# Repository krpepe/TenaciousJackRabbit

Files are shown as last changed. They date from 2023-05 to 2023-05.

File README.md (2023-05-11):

# Tenacious Jack Rabbit

*__This is still a work in progress!__* <br>
<br>
I have everything assembled but have not set up the config yet. I am hoping to have that done by 5-11-23. I have printed all of the parts that I redesigned and they all fit snuggly. If you decide to try this please let me know if you encounter any issues. I will attempt to correct any issues that come up. I will be updating as necessary. I have included Gearbox front, filament block and filament blocks end with supports incase someones printer can't successfully print it without. I printed mine without supports and had very minamal cleanup to get them to fit.

This is based on the awesome work of EtteGit https://github.com/EtteGit/EnragedRabbitProject. I also found inspiration from the awesome work of sneakytreesnake (https://github.com/sneakytreesnake/SturdyBunnyProject).

# Motivation

After doing some research before building the ERCF I found a lot of people saying there was flex in the assembly that was causing issues with operation. The suggestion was to go with the SturdyBunnyProject. This added a 2020 extrusion in place of the 5mm threaded rods. The only down side to this design in my opinion was it changed the print orientation of the filament block from upright to laying sideways which then required supports to print the filament blocks. I decided to change the location of the 2020 extrusion to allow printing the filament block in the designed orientation to be able to print without supports.

# Changes to BOM

|Qty|Description|
|:---:|---|
|1|2020 Extrusion one end with M6 taped hole (1)|
|1|M6x10 BHCS|
|2|M3 T-nuts (2)|
|7|M3x8 SHCS (2)|
|3|M5 T-nuts|
|3|M5x10 BHCS|

* (1) 171mm for 6, 234mm for 9 and 297mm for 12. These are minimum lengths, can be longer if you want.
* (2) Only needed for mounting Fysetc ERB V1.1 to 2020 exrtusion

# Assembly

To assemble you have to attach the 2020 extrusion to the Gearbox_Front_2020_Mount with the M6x10 before assembling the gearbox. The filament blocks and bearing blocks slide on to the 2020 extrusion instead of the 5mm rods in the assembly manual. The Filament_Blocks_End goes on after the last filament block and should be tight against the last filament block. 2 M5 BHCS and M5 T-nuts attach it to the 2020 extrusion. There should be no air gaps between the gearbox front and the Filament Blocks End.

# Assembly Pics





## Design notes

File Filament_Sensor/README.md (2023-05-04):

Readme for Filament Sensor

Clockwoork 2 with 3mm ball bearing, 3mm rod and micro switch.

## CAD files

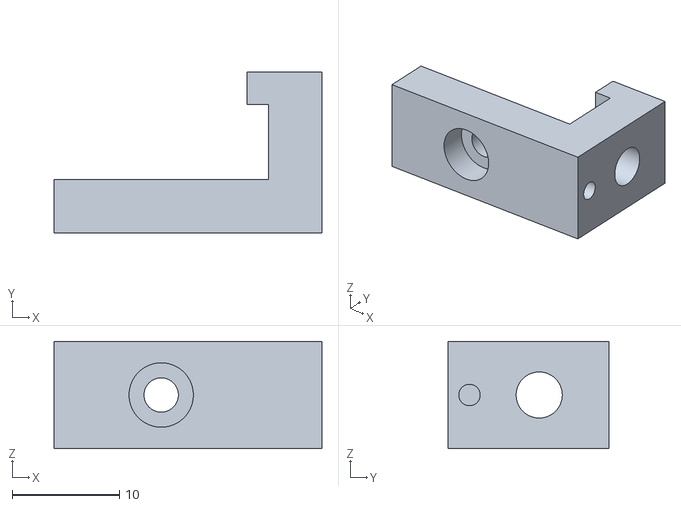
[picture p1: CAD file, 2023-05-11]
Carrot_Feeder/Stls/2020/Fysect_ERB_V1.1_2020_Mount.stl
25.0 x 15.0 x 10.0

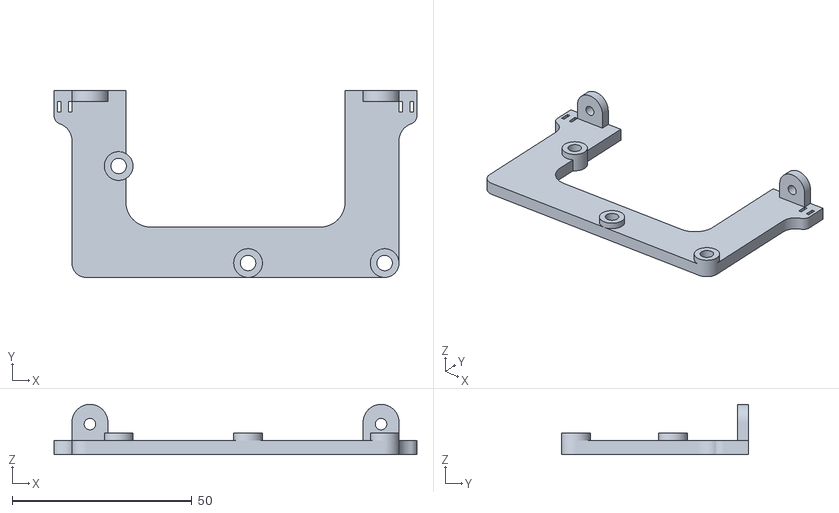
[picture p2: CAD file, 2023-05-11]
Carrot_Feeder/Stls/2020/erb_holder_x2.stl
101.0 x 52.0 x 14.0

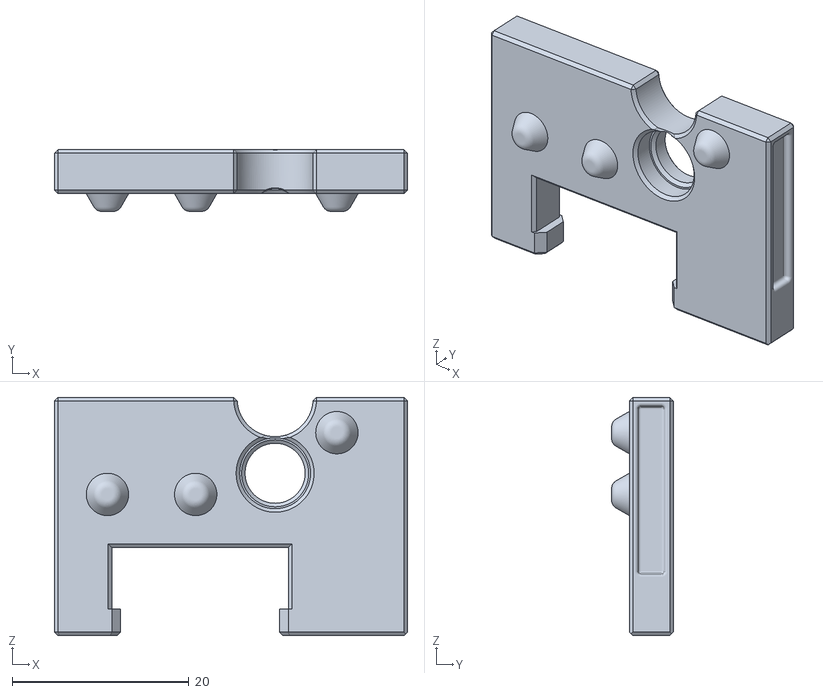
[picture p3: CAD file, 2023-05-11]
Carrot_Feeder/Stls/2020/Bearing insert 2020 mount v3.stl
40.0 x 7.00 x 27.0

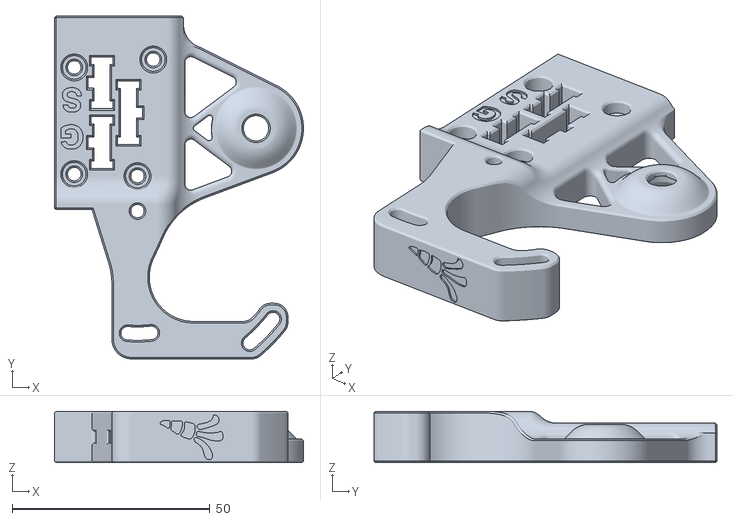
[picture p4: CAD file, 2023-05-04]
Carrot_Feeder/Stls/2020/M4 Gear Arm 2020 mount v4.stl
63.0 x 86.7 x 13.0

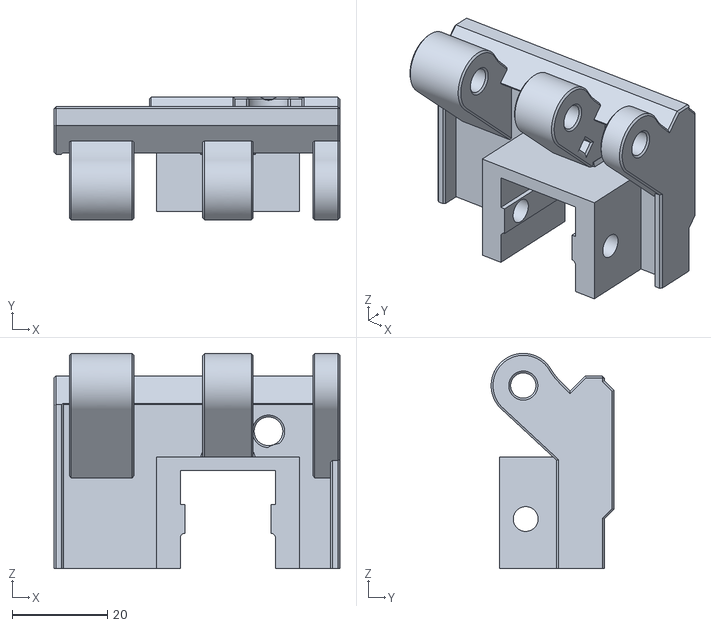
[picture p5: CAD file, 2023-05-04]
Carrot_Feeder/Stls/2020/Filament blocks end 2020 mount v11.stl
60.0 x 25.7 x 45.1

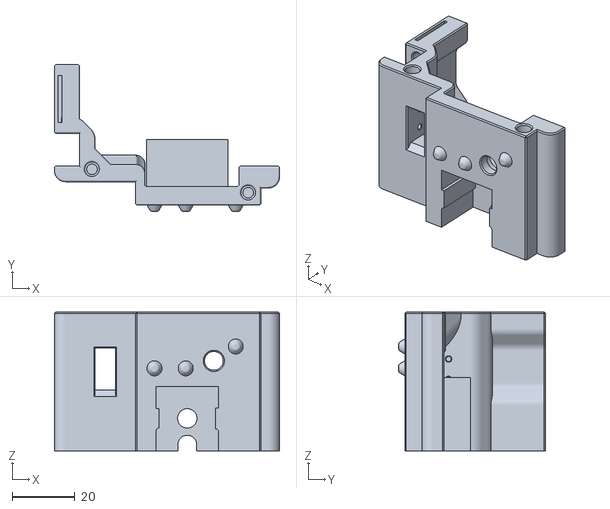
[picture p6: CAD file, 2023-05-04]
Carrot_Feeder/Stls/2020/Gearbox Front 2020 Mount v13.stl
72.0 x 47.0 x 44.4

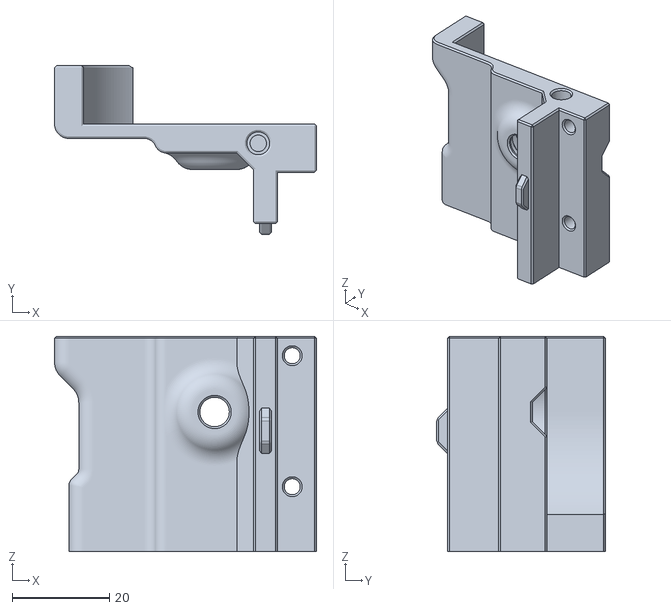
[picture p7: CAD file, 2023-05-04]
Carrot_Feeder/Stls/2020/Gear box mount rear 2020 v6.stl
54.0 x 34.8 x 44.4

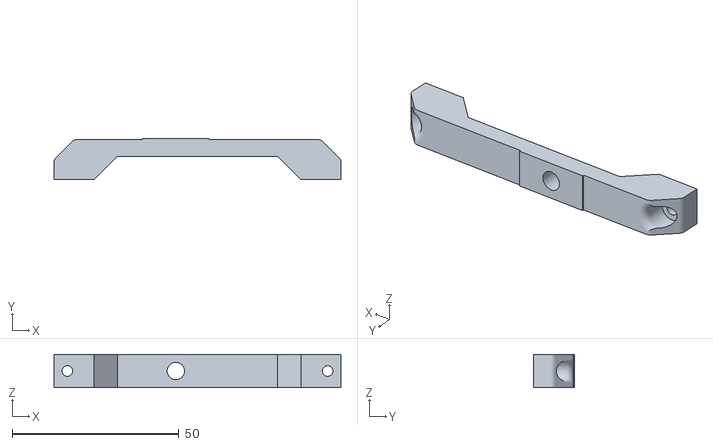
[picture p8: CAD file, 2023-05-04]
Carrot_Feeder/Stls/2020/Outside foot v5.stl
86.0 x 12.4 x 10.0

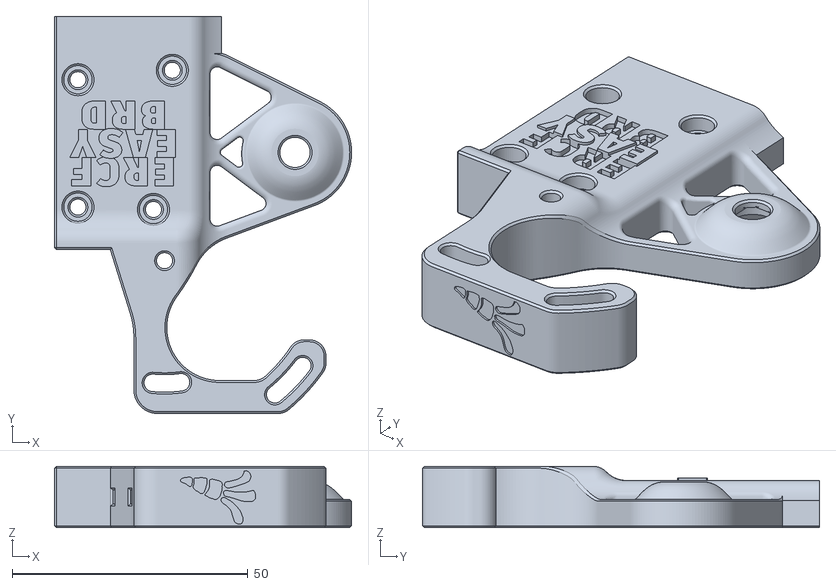
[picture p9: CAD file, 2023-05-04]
Carrot_Feeder/Stls/2020/Motor_Arm_NEMA14_EASYBRD v2.stl
63.0 x 84.1 x 13.0

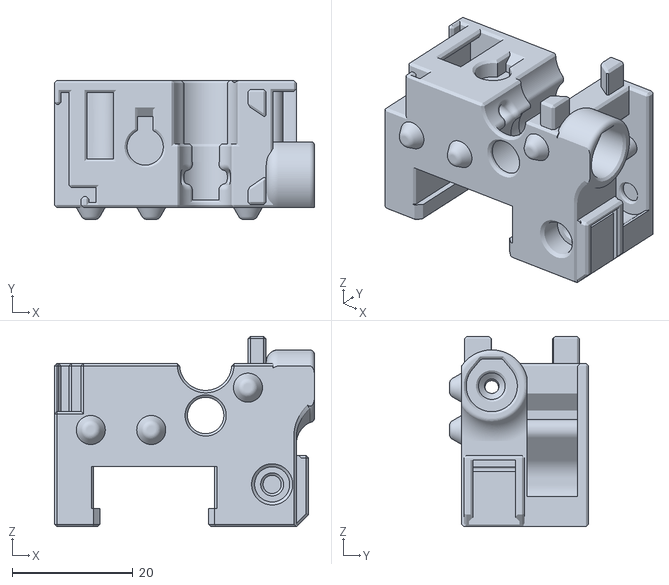
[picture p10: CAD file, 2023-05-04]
Carrot_Feeder/Stls/2020/Filament block 2020 mount v10.stl
43.0 x 23.0 x 31.5

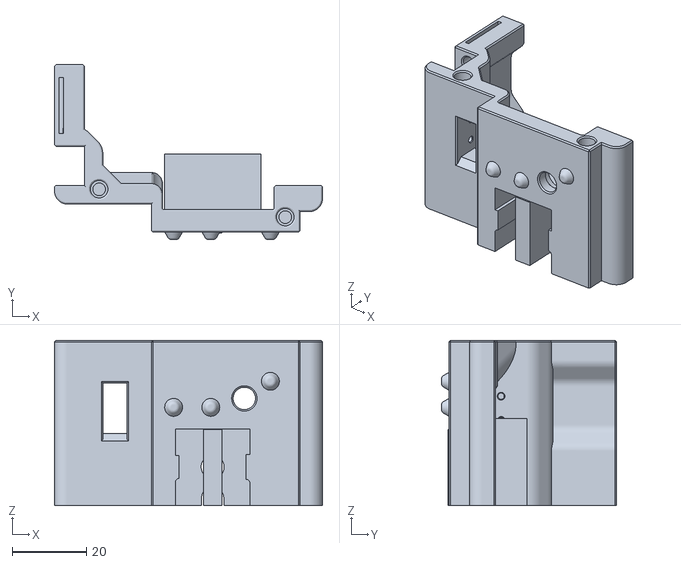
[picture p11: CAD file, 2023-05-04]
Carrot_Feeder/Stls/2020/Gearbox_Front_2020_Mount_v13_w_support.stl
72.0 x 47.0 x 44.4

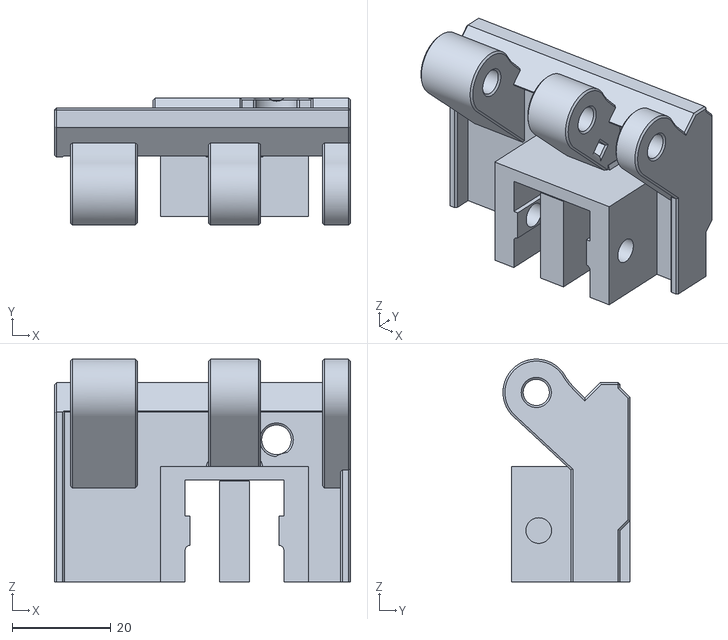
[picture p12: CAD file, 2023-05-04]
Carrot_Feeder/Stls/2020/Filament_blocks_end_2020_mount_v11_w_support.stl
60.0 x 25.7 x 45.1

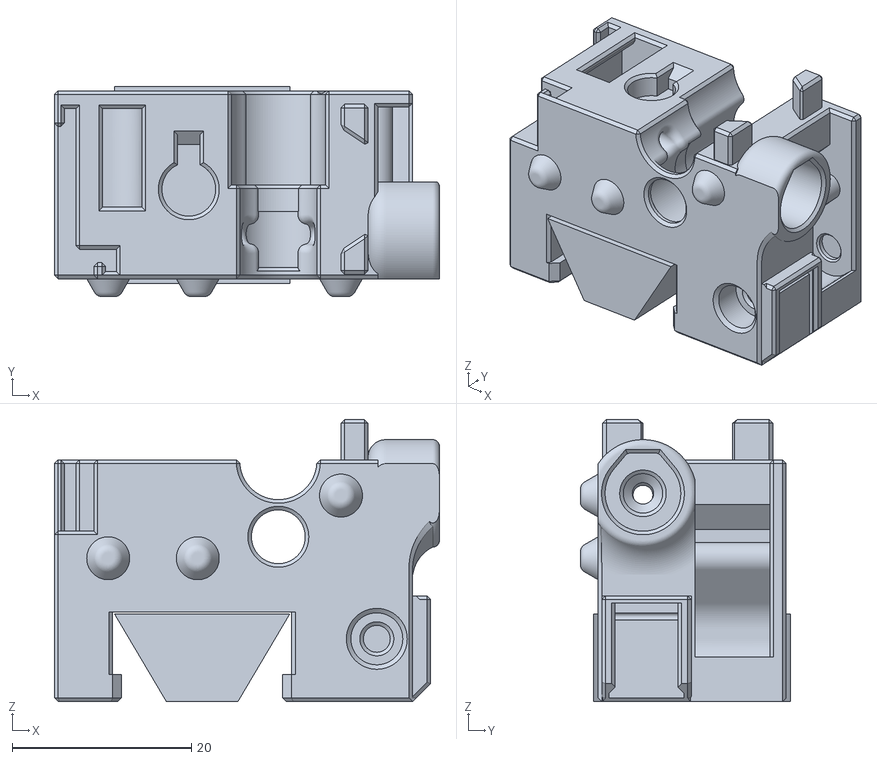
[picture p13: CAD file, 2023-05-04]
Carrot_Feeder/Stls/2020/Filament_block_2020_mount v10_w_support.stl
43.0 x 23.5 x 31.5

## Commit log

2023-05-04 Add files via upload
    Added files changed for 2020 mount
    [Filament block 2020 mount v10.stl, Filament blocks end 2020 mount v11.stl, Filament_block_2020_mount v10_w_support.stl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]
2023-05-04 Create enraged rabbit feeder 2020 assembly v35.f3z
2023-05-11 Create Bearing insert 2020 mount v3.stl
    [Bearing insert 2020 mount v3.stl]
